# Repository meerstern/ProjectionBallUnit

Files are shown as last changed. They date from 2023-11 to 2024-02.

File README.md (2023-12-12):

# 簡易レーザープロジェクタ ProjectionBall Unit

## 概要 
  * ロボット制御技術を応用したガルバノスキャナ方式の簡易レーザープロジェクタです  
  * 文字や時刻、日時、内蔵図形を描画することが可能です  
  * 本体ボタン、PCのCOMポートやUARTを介して設定を変更することが可能です  
  * 任意の文字列は英数字を最大5文字同時表示、それ以上は32文字までスクロール表示可能です  
  * 投影距離は明るい場所で数m以下、暗い場所で10m以下が目安です  
  * Pico-SDKを使用したソースコードを公開しています  

## 仕様  
  * 電源スイッチ、モード切替、パターン切替、BOOTボタン、RESETボタンを搭載しています  
  * マイコンRP2040、RTC SD3077、モータFA-130、ドライバTB6612、エンコーダMA732Qを使用しています    
  * 赤色レーザーモジュール(出力1mW以下、ClassⅡ同等品)  
  * 5V/0.8AのUSB電源(micro USB)で動作  
  * 電源LED(青)、エラーLED(オレンジ)を搭載  
  * 時刻(RTC)/設定データ一時保存用電池 CR1220  
  * シリアルポートP1 ボーレート9600bps、データサイズ8bit、パリティ無、ストップ1bitが既定値
  * サイズ60mm x60mm x 43mm(突起部、USBコネクタ除く)、固定穴45mm x45mm M3x4

## アプリケーション例
  * 移動ロボットに組込して進路を表示  
  * イベント等での情報を表示  

## 注意点
  * この製品はclassⅡのレーザーを使用しています  
  * レーザーを使用しているため、光源を直視しないでください
  * 分解や改造をした状態で使用すると非常に危険ですので、お控えください  
  * この製品によって引き起こされることについては、当社は責任を持ちません  
  * 目にレーザー光が入る可能性があるため、人や動物に対して投影しないでください    
  * 汎用モータを使用しているため、描画のちらつきや崩れがあります    
  * ガルバノミラーはガラス製表面鏡のため、怪我をする恐れがあります 手を触れなでください  
  * 光軸がずれる可能性があるため、落下や衝撃を与えないでください  
  * 本製品は研究、開発目的の用途を想定しています  
  * 起動後にエラーLEDが点灯する場合はミラー部分が回転できるか、引っかかりがないか確認し、電源を入れ直してください    
  * 告知なしに部品や仕様を変更する場合があります  

## 使い方
### a.単体で使用する場合  
　microUSBをUSB電源等に接続し、電源スイッチ、モード切替、パターン切替スイッチで操作することが可能です    

### b.他の機器と連携する場合  
　microUSBをUSB電源等に接続し、P1端子を介してUART通信(ボーレート9600bps, 3.3V)可能です  
  マイコン等からコマンドを送信して制御することが可能です  

### c.設定を行う場合
　PC等にmicroUSBを接続し、Teraterm等からシリアルポートを介してコマンドで設定を行うことが可能です  

### d.ファームウェアの書換を行う場合
　PC等にmicroUSBを接続し、BOOTボタンを押した状態でRSTボタンを押すとUSBドライブとして認識されます  
  ファームウェアファイル(*.uf2)を認識されたUSBドライブに書き込むことでファームの書換が可能です  

## 描画モード

  * パターン0: 星
  * パターン1: 矢印
  * パターン2: メール
  * パターン3: スマイル
  * パターン4: 太陽
  * パターン5: 雲
  * パターン6: 傘
  * パターン7: 雪だるま
  * パターン8: 雲と雷
  * パターン9: ハート  

## 描画パターン   
  * モード0: 通常描画
  * モード1: 一筆書き描画
  * モード2: 回転描画
  * モード3: デジタル時計
  * モード4: デジタル日付
  * モード5: 任意メッセージ  
※メッセージは英数字、最大5文字、それ以上はスクロール表示です  

## 描画例
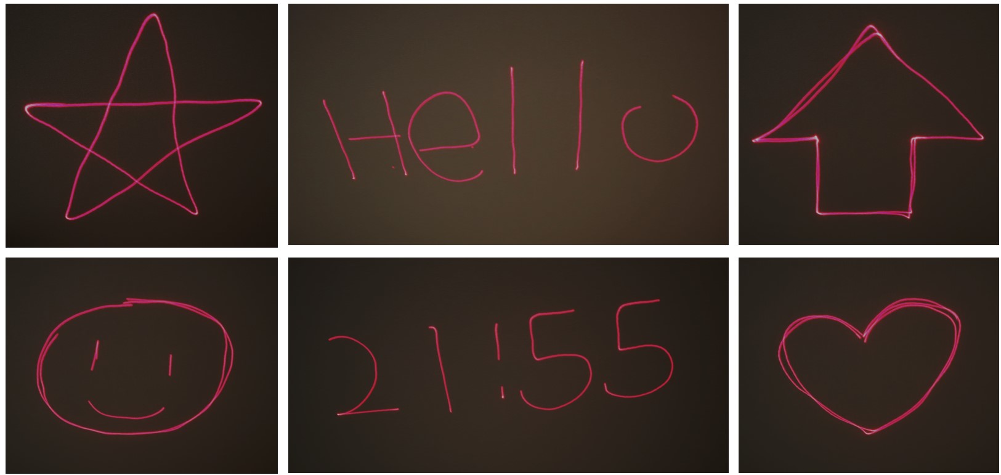
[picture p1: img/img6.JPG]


## 各部機能
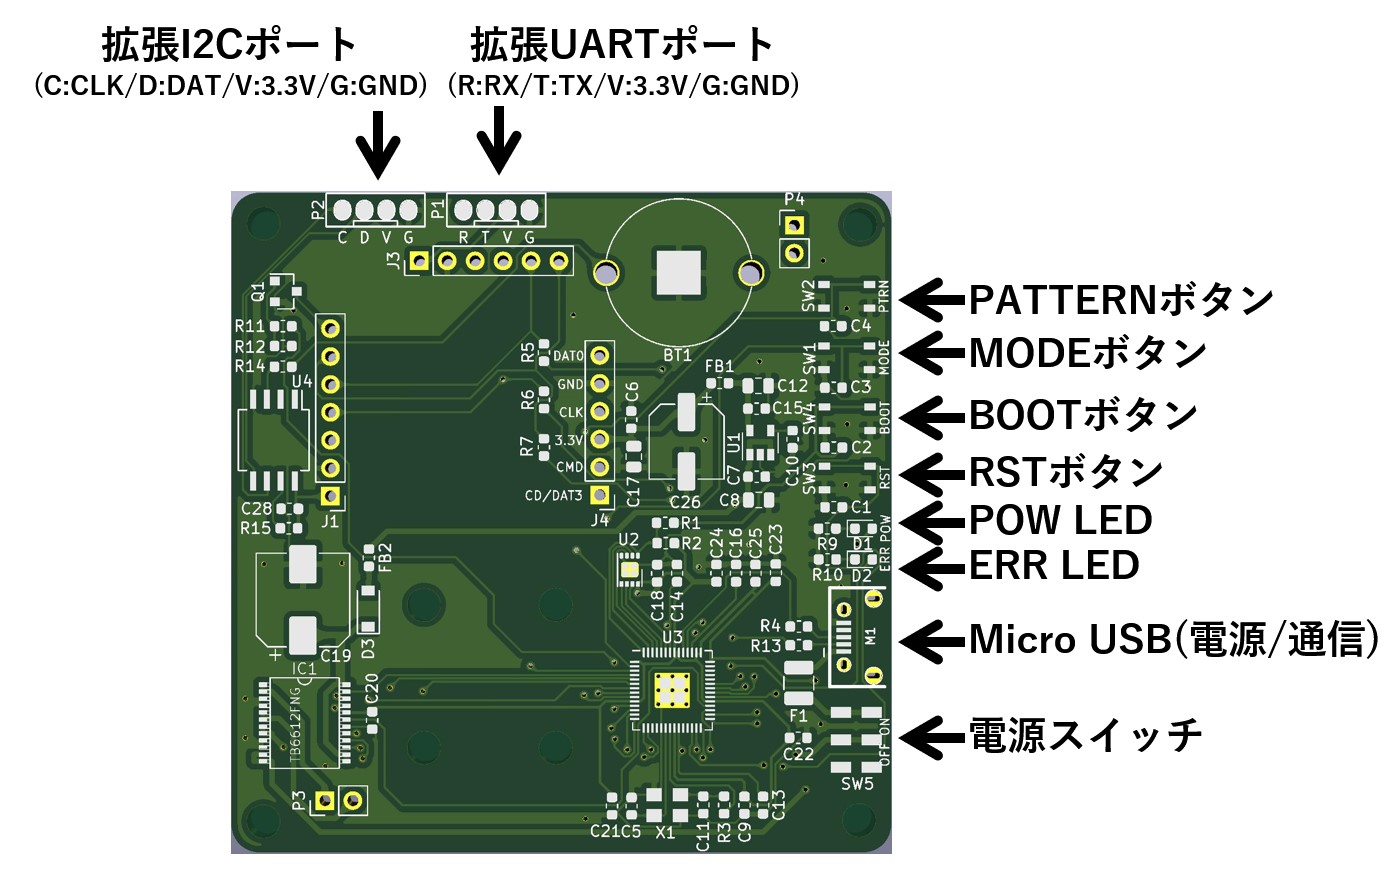
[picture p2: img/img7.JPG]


## コマンド
  * コマンド文字列を送信することで描画モードやパターン等の設定が可能です  
  * 改行コードは"\r\n"がデフォルトです  

### 日時設定コマンド  
| コマンド名 | コマンド | 引数 | 例 | 
|:---|:---|:---|:---|
| 時刻設定 | tim= | hhmmss | tim=220212(Enterキー) |
| 時刻確認 | tim? | なし | tim?(Enterキー) |
| 日時設定 |	day= | YYMMDD | day=220305(Enterキー) | 
| 日時確認 |	day? | なし | day?(Enterキー) | 	

※日付時刻は必ずそれぞれ2桁で入力してください  
　例　2時8分01秒→tim=020801 

### 制御コマンド  
| コマンド名 | コマンド | 引数 | 例 | 
|:---|:---|:---|:---|
| モード確認 |	mod? | なし | mod?(Enterキー) | 
| モード設定 |	mod= | モード | mod=1(Enterキー) | 
| パターン確認 |	ptn? | なし | ptn?(Enterキー) | 
| パターン設定 |	ptn= | パターン| ptn=2(Enterキー) | 
| ソフトリセット | rst! | なし | rst!(Enterキー) |  
| 描画一時停止 | pus! | なし | pus!(Enterキー) |
| 描画再開 |	rsm! | なし | rsm!(Enterキー) | 
| 描画角設定 |	deg= | 角度 | deg=90(Enterキー) | 	
| 描画角確認 |	deg? | なし | deg?(Enterキー) | 	

※描画角は描画の上下左右等の角度を変更する場合に使用します  
※描画角のデフォルトは0度(deg=0)です  

### ユーザ設定コマンド  
| コマンド名 | コマンド | 引数 | 例 | 
|:---|:---|:---|:---|
| 描画文字列確認 |	str? | なし | str?(Enterキー) | 
| 描画文字列設定(MEM) |	str= | 英数字 | str=Hello(Enterキー) | 
| 描画文字列設定(RAM) |	stg= | 英数字 | stg=Hello(Enterキー) |  

※MEMの場合、文字列はメモリに保存され、自動的に再起動します  
※RAMの場合、文字列は即時反映されますが、電源再投入等でメモリに保存された文字列に戻ります  

### タイマ設定コマンド  
| コマンド名 | コマンド | 引数 | 例 | 
|:---|:---|:---|:---|
| タイマ確認 |	tst? | なし | tst?(Enterキー) | 
| タイマ有効化 | ten! | なし | ten!(Enterキー) |  
| タイマ無効化 | tds! | なし | tds!(Enterキー) |
| 停止時刻確認 |	pus? | なし | pus?(Enterキー) | 
| 停止時刻設定 |	pus= | hhmm | pus=1230(Enterキー) | 
| 再開時刻確認 |	rsm? | なし | pus?(Enterキー) | 
| 再開時刻設定 |	rsm= | hhmm | pus=1530(Enterキー) | 

※タイマ確認は0で無効状態、1で有効状態を示しています  

### キャリブレーションコマンド  
| コマンド名 | コマンド | 引数 | 例 | 
|:---|:---|:---|:---|
| 描画中心確認 |	cen? | なし | cen?(Enterキー) | 
| 描画中心設定 |	cen= | X,Y | cen=100,-200(Enterキー) | 

※レーザーが基板や筐体に当たって描画が隠れてしまう場合にのみ、描画中心を調整します  
※描画中心のキャリブレーション値は出荷時に調整しています    
※キャリブレーション値は初期値に対してX軸(縦方向)、Y軸(横方向)のオフセット値を設定します  

### エラーLED点灯時の確認
  * 起動後にエラーLEDが点灯する場合はミラー部分が回転できるか、引っかかりがないか確認し、電源を入れ直してください
  * ミラーが回転して描画を開始しない場合は下記の図のようにミラーの角度を調整して電源を入れ直してください
  * 手前から見てレーザーモジュールからの光がX軸ミラー、Y軸ミラーの2つのミラーに反射する角度に調整します  
  * ミラーはガラス製のため、怪我の恐れがあります  手を触れないように注意してください   
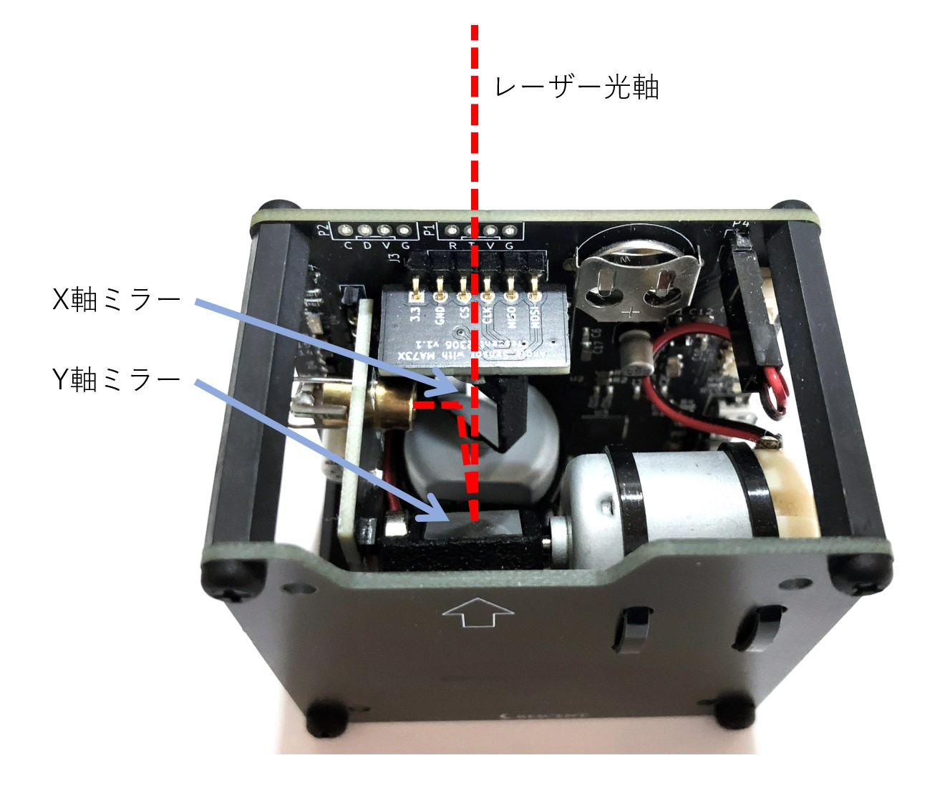
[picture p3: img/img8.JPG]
  

### 電池交換時の確認
  * RTC電池は電源供給なしで3年以上、日時、時刻及び設定情報を保持することが可能です
  * 万一、保持できなくなった場合はCR1220の電池交換を行ってください
  * 設定情報はモード、パターン、タイマ状態、描画角を保持しています
  * 電池交換後は日時、時刻及び設定情報が不定値となるため、必ず時刻、日付、モード、パターン、タイマ状態、描画角を再設定してください  
  * 特に描画角が不定値になると正しく描画されません deg=0(Enterキー)とコマンドを入力して設定してください

## 外観
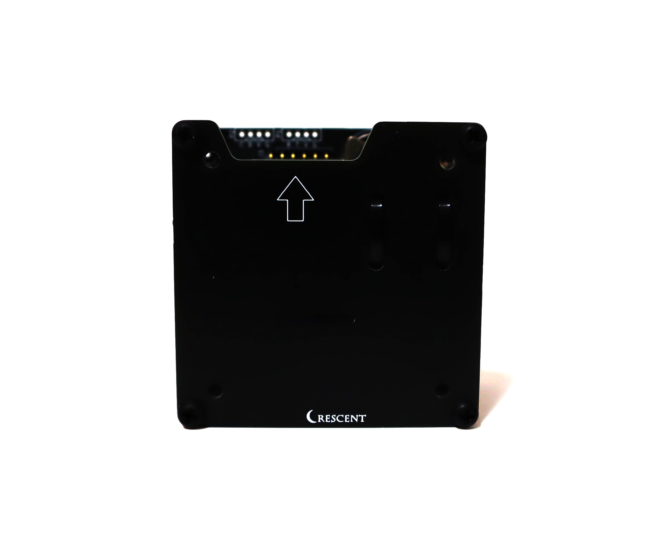
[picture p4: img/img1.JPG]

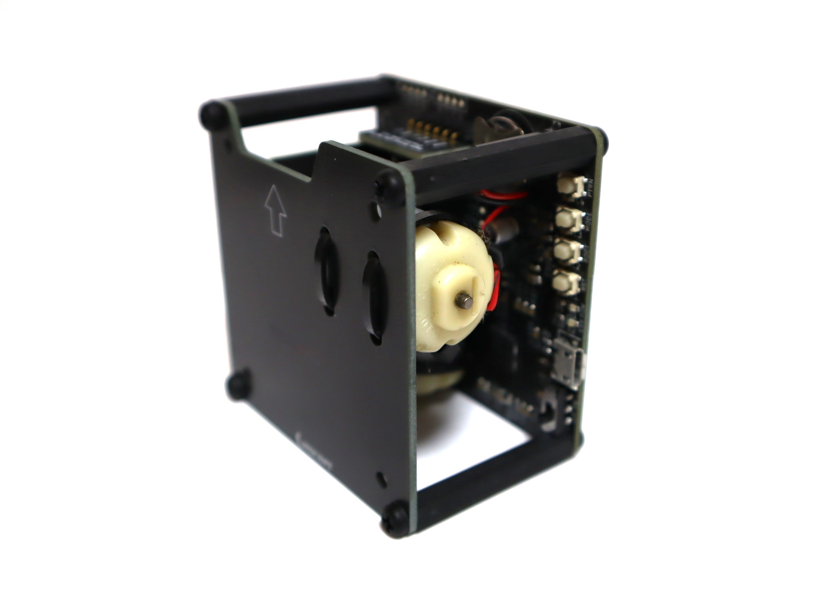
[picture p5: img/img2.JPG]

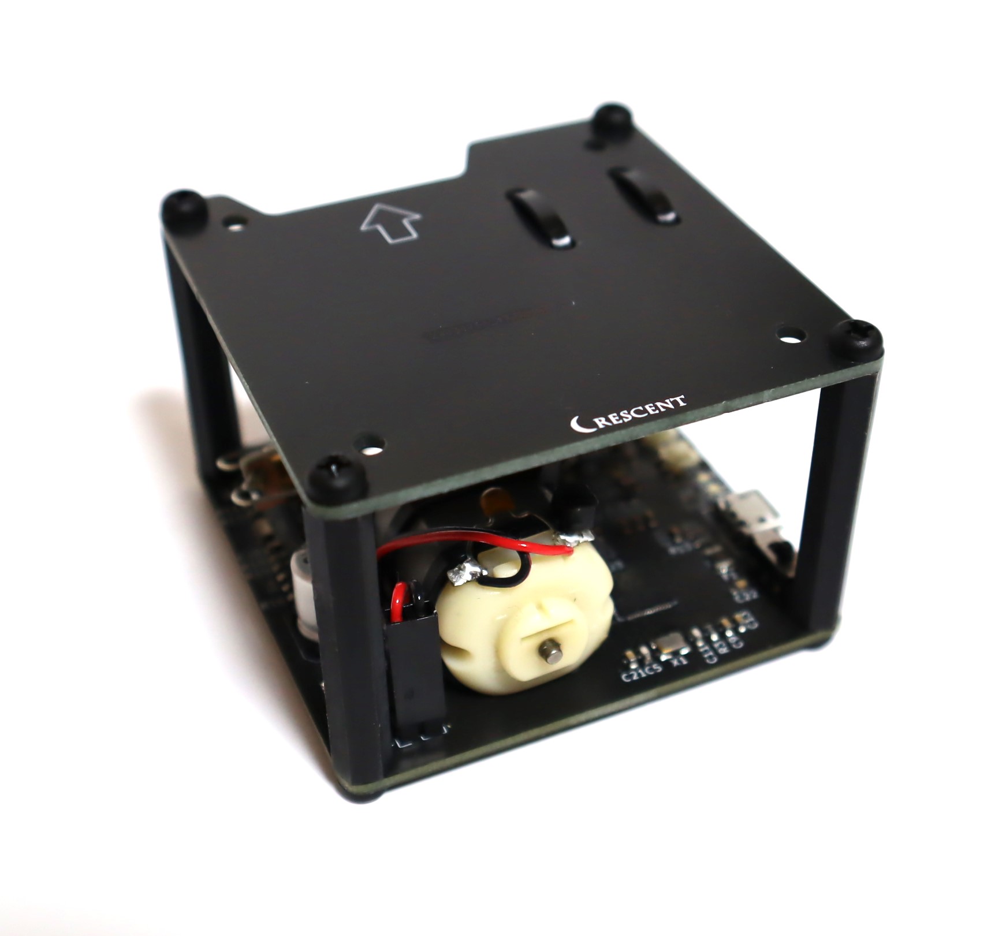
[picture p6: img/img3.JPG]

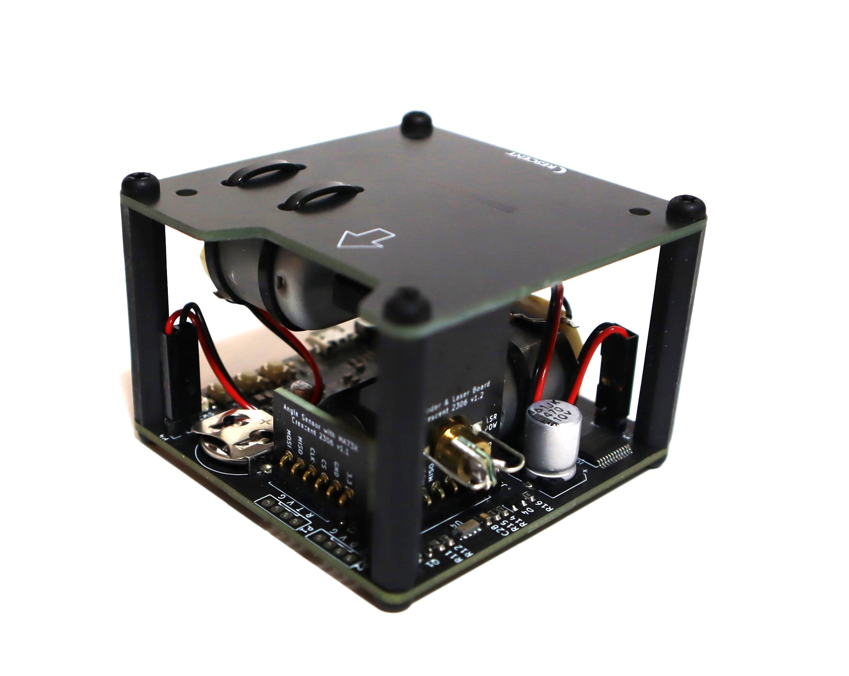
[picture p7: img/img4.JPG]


License - MIT

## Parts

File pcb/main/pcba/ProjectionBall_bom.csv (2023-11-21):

Comment | Designator | Footprint | LCSC part number | Stock
SW_DPDT_x2 | SW5 | DPDT_SMD_Large | C115375
SD3077 | U4 | SO-8_5.3x6.2mm_P1.27mm | C4748679
27 | R7,R6,R5,R13,R4 | R_0603_1608Metric | C227752
100u | C26 | CP_Elec_6.3x3.9 | C2963046
Q_NMOS_GSD | Q1 | SOT-23 | C2991132
Ferrite_Bead_Small | FB2,FB1 | L_0603_1608Metric | C80165
10u | C17,C12,C8 | C_0805_2012Metric | C380332
0.1u | C14,C28,C25,C24,C23,C22,C21,C18,C13,C9,C2,C1,C3,C4,C6,C7,C15,C20 | C_0603_1608Metric | C56476
W25Q16JVUX | U2 | SON-8-1EP_3x2mm_P0.5mm_EP1.4x1.6mm | C2843335
RP2040 | U3 | RP2040-QFN-56 | C2040
12MHz | X1 | FA238V | C2901650
SW_Push | SW4,SW3,SW1,SW2 | SKRPACE010 | C115360
10k | R15,R2,R12 | R_0603_1608Metric | C209220
330 | R14 | R_0603_1608Metric | C103548
1k | R3,R1,R9,R10,R11 | R_0603_1608Metric | C73797
2.2u | C16 | C_0603_1608Metric | C2691406
10p | C11,C5 | C_0603_1608Metric | C388068
0.01u | C10 | C_0603_1608Metric | C307346
470u | C19 | CP_Elec_8x10 | C2827943
POW_LED | D1 | LED_0603_1608Metric | C89814
ERR_LED | D2 | LED_0603_1608Metric | C90692
Fuse | F1 | R_1210_3225Metric | C20805
TB6612FNG | IC1 | tb6612-SSOP24 | C141517
MICRO-USB-SHIELD-ZX62R-B-5P | M1 | CONN-10118194-0001LF-FCI | C132563
LD3985M33R | U1 | SOT-23-5 | C46243
D | D3 | D_SOD-123 | C129191

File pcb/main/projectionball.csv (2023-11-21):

ID | 参照記号 | パッケージ | 数 | 名称 | Supplier and ref
1 | SW5 | DPDT_SMD_Large | 1 | SW_DPDT_x2
2 | U4 | SO-8_5.3x6.2mm_P1.27mm | 1 | SD3077
3 | R7,R6,R5,R13,R4 | R_0603_1608Metric | 5 | 27
4 | C26 | CP_Elec_6.3x3.9 | 1 | 100u
5 | Q1 | SOT-23 | 1 | Q_NMOS_GSD
6 | J4 | PinHeader_1x06_P2.54mm_Vertical | 1 | microTF
7 | FB2,FB1 | L_0603_1608Metric | 2 | Ferrite_Bead_Small
8 | P2 | GROVE | 1 | GROVE_I2C
9 | P1 | GROVE | 1 | GROVE_UART
10 | P4 | PinHeader_1x02_P2.54mm_Vertical | 1 | MOTOR2
11 | J1 | PinHeader_1x07_P2.54mm_Vertical | 1 | Conn_01x07
12 | C17,C12,C8 | C_0805_2012Metric | 3 | 10u
13 | C14,C28,C25,C24,C23,C22,C21,C18,C13,C9,C2,C1,C3,C4,C6,C7,C15,C20 | C_0603_1608Metric | 18 | 0.1u
14 | U2 | SON-8-1EP_3x2mm_P0.5mm_EP1.4x1.6mm | 1 | W25Q16JVUX
15 | U3 | RP2040-QFN-56 | 1 | RP2040
16 | X1 | FA238V | 1 | 12MHz
17 | SW4,SW3,SW1,SW2 | SKRPACE010 | 4 | SW_Push
18 | R15,R2 | R_0603_1608Metric | 2 | 10k
19 | R14 | R_0603_1608Metric | 1 | 330
20 | R3,R1,R9,R10,R11 | R_0603_1608Metric | 5 | 1k
21 | C16 | C_0603_1608Metric | 1 | 2.2u
22 | C11,C5 | C_0603_1608Metric | 2 | 10p
23 | BT1 | 2895 | 1 | CR1220
24 | REF3,REF4,REF2,REF1,REF12,REF11,REF10,REF9 | MountingHole_3mm | 8 | MountingHole_3mm
25 | C10 | C_0603_1608Metric | 1 | 0.01u
26 | C19 | CP_Elec_8x10 | 1 | 470u
27 | D1 | LED_0603_1608Metric | 1 | POW_LED
28 | D2 | LED_0603_1608Metric | 1 | ERR_LED
29 | F1 | R_1210_3225Metric | 1 | Fuse
30 | IC1 | tb6612-SSOP24 | 1 | TB6612FNG
31 | J3 | PinHeader_1x06_P2.54mm_Vertical | 1 | ENC1
32 | M1 | CONN-10118194-0001LF-FCI | 1 | MICRO-USB-SHIELD-ZX62R-B-5P
33 | P3 | PinHeader_1x02_P2.54mm_Vertical | 1 | MOTOR1
34 | R12 | R_0603_1608Metric | 1 | 20k
35 | U1 | SOT-23-5 | 1 | LD3985M33R
36 | D3 | D_SOD-123 | 1 | D

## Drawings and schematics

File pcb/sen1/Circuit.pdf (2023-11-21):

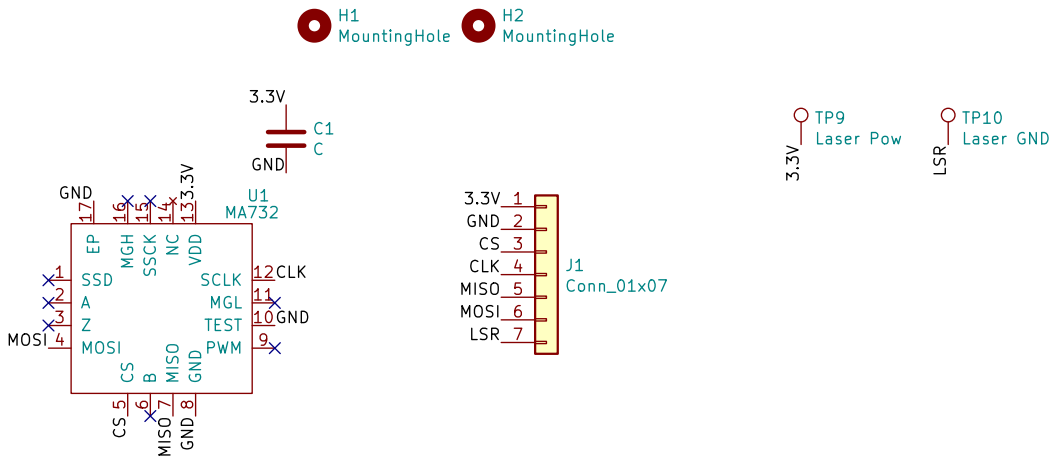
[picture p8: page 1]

CS CLK MISO MOSI C1 C GND

File: ma73x.sch Sheet: / Crescent

Id: 1/1 Title: ProjectionBall Encoder & Laser Board

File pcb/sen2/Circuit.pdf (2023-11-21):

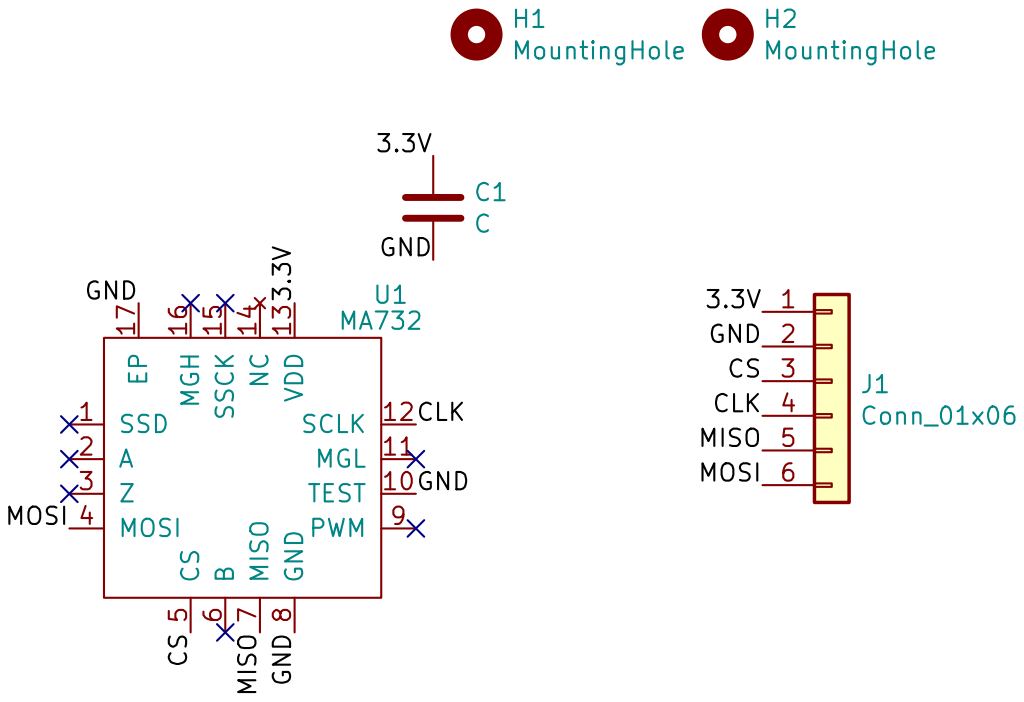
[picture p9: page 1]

CS CLK MISO MOSI C1 C GND

File: ma73x.sch Sheet: / Crescent

Id: 1/1 Title: Angle Sensor Board with MA732

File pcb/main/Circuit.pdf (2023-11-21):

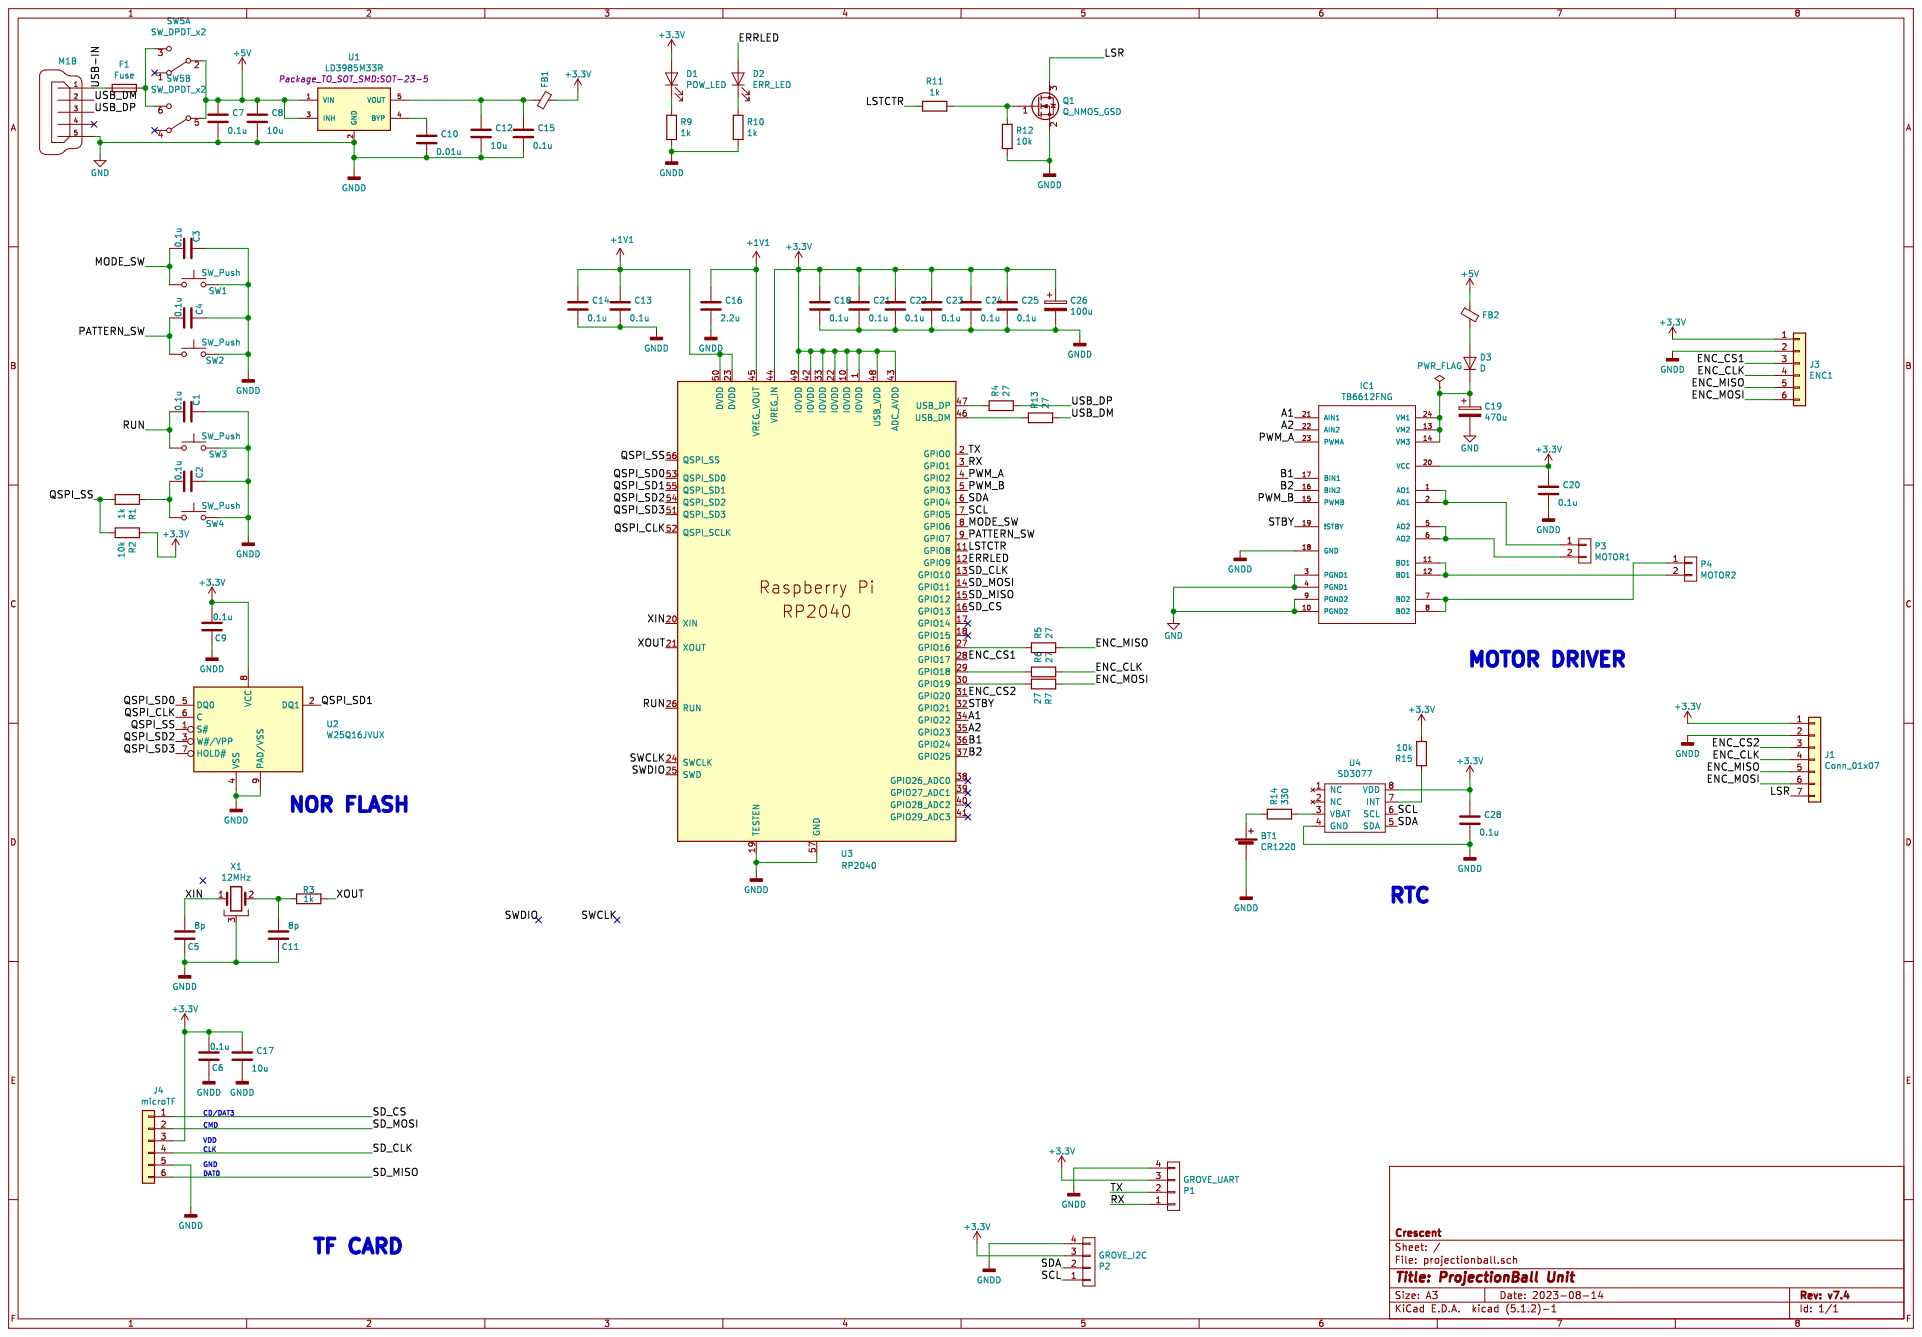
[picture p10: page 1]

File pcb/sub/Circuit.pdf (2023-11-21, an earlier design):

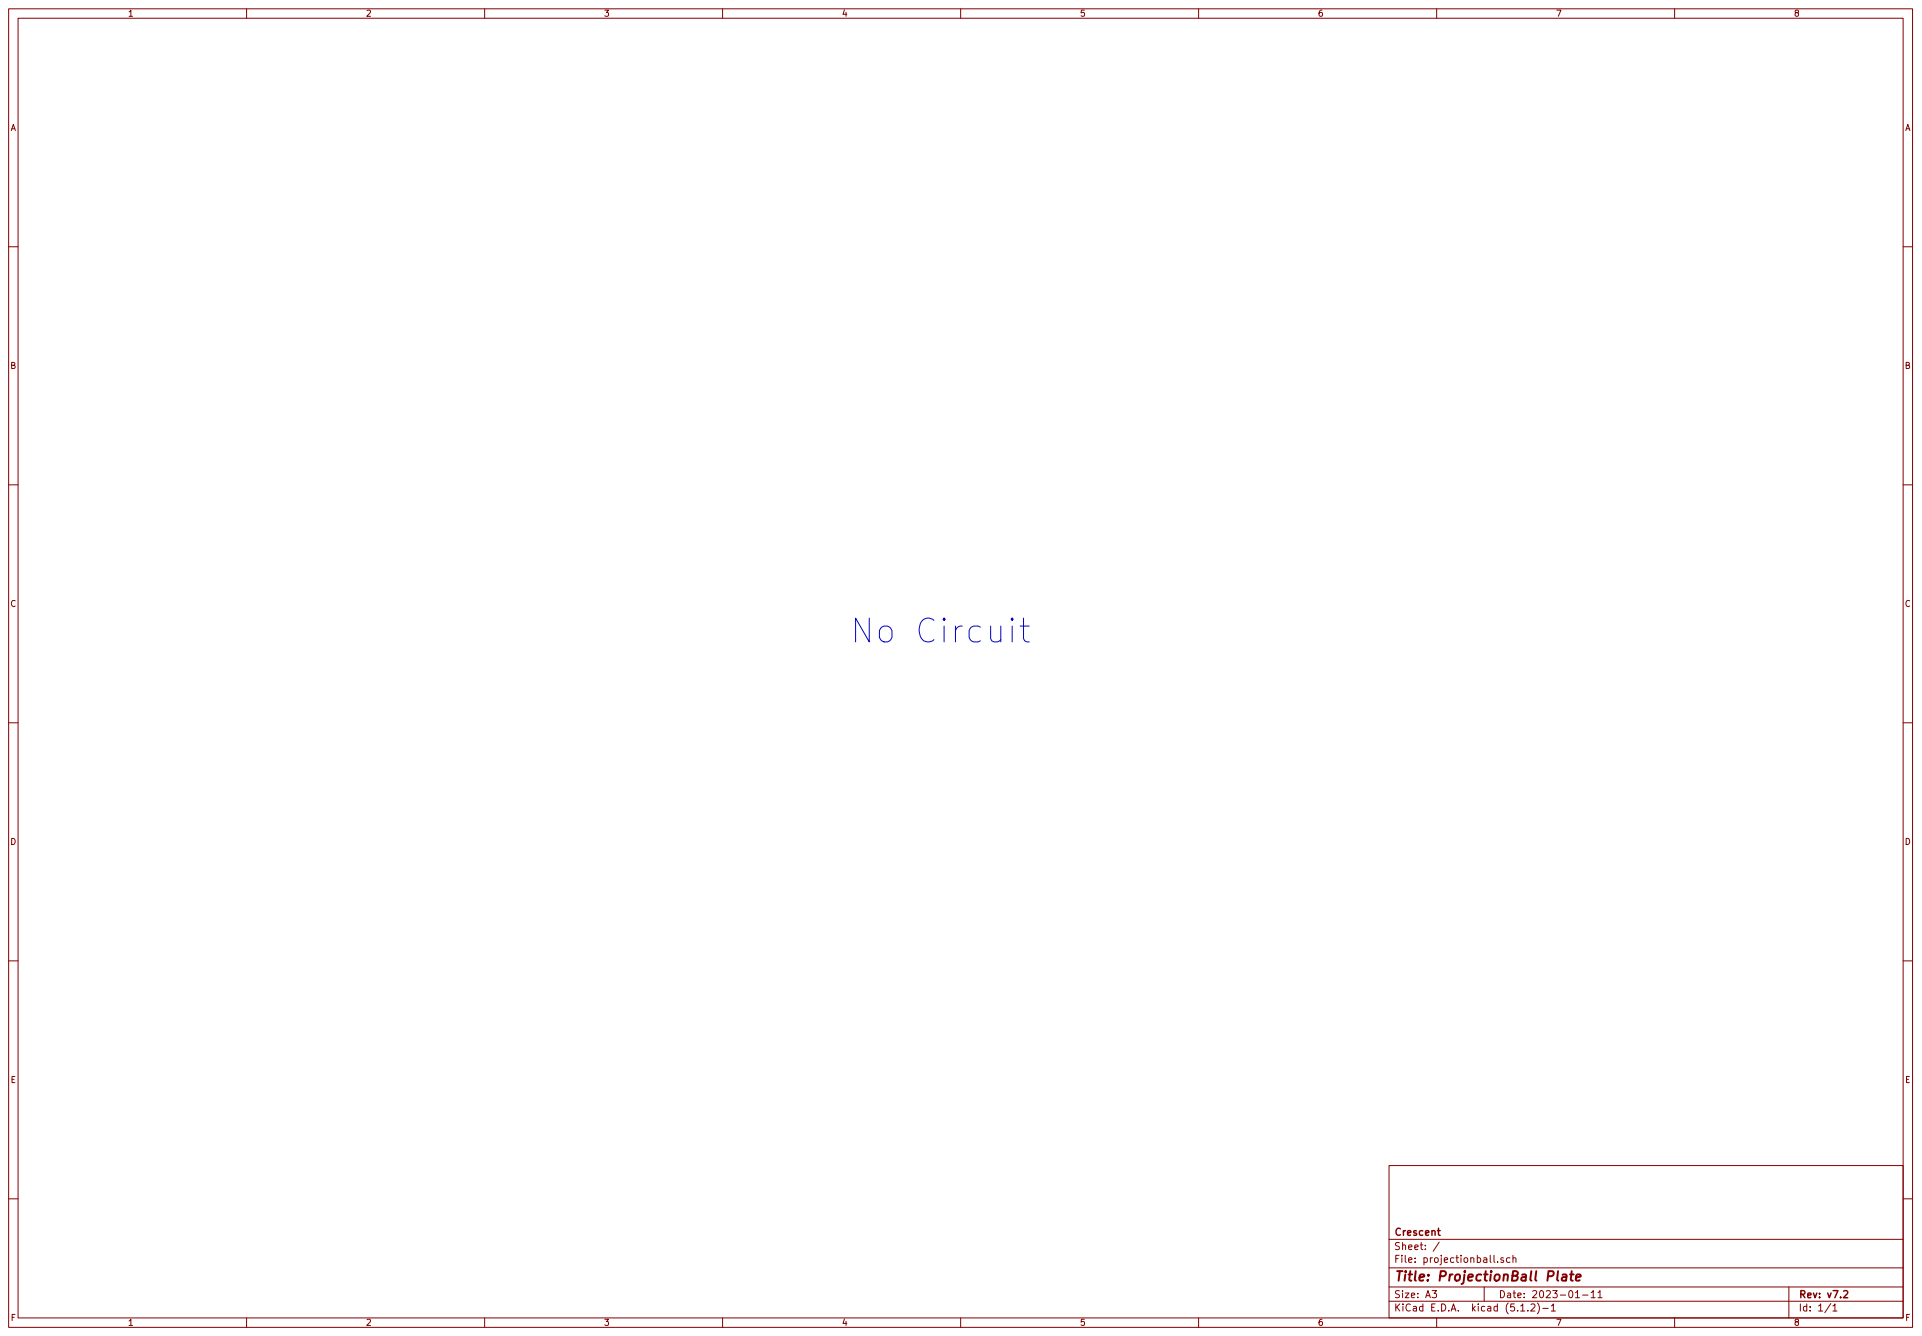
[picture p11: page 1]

File: projectionball.sch Sheet: / Crescent No Circuit

Id: 1/1 Title: ProjectionBall Plate

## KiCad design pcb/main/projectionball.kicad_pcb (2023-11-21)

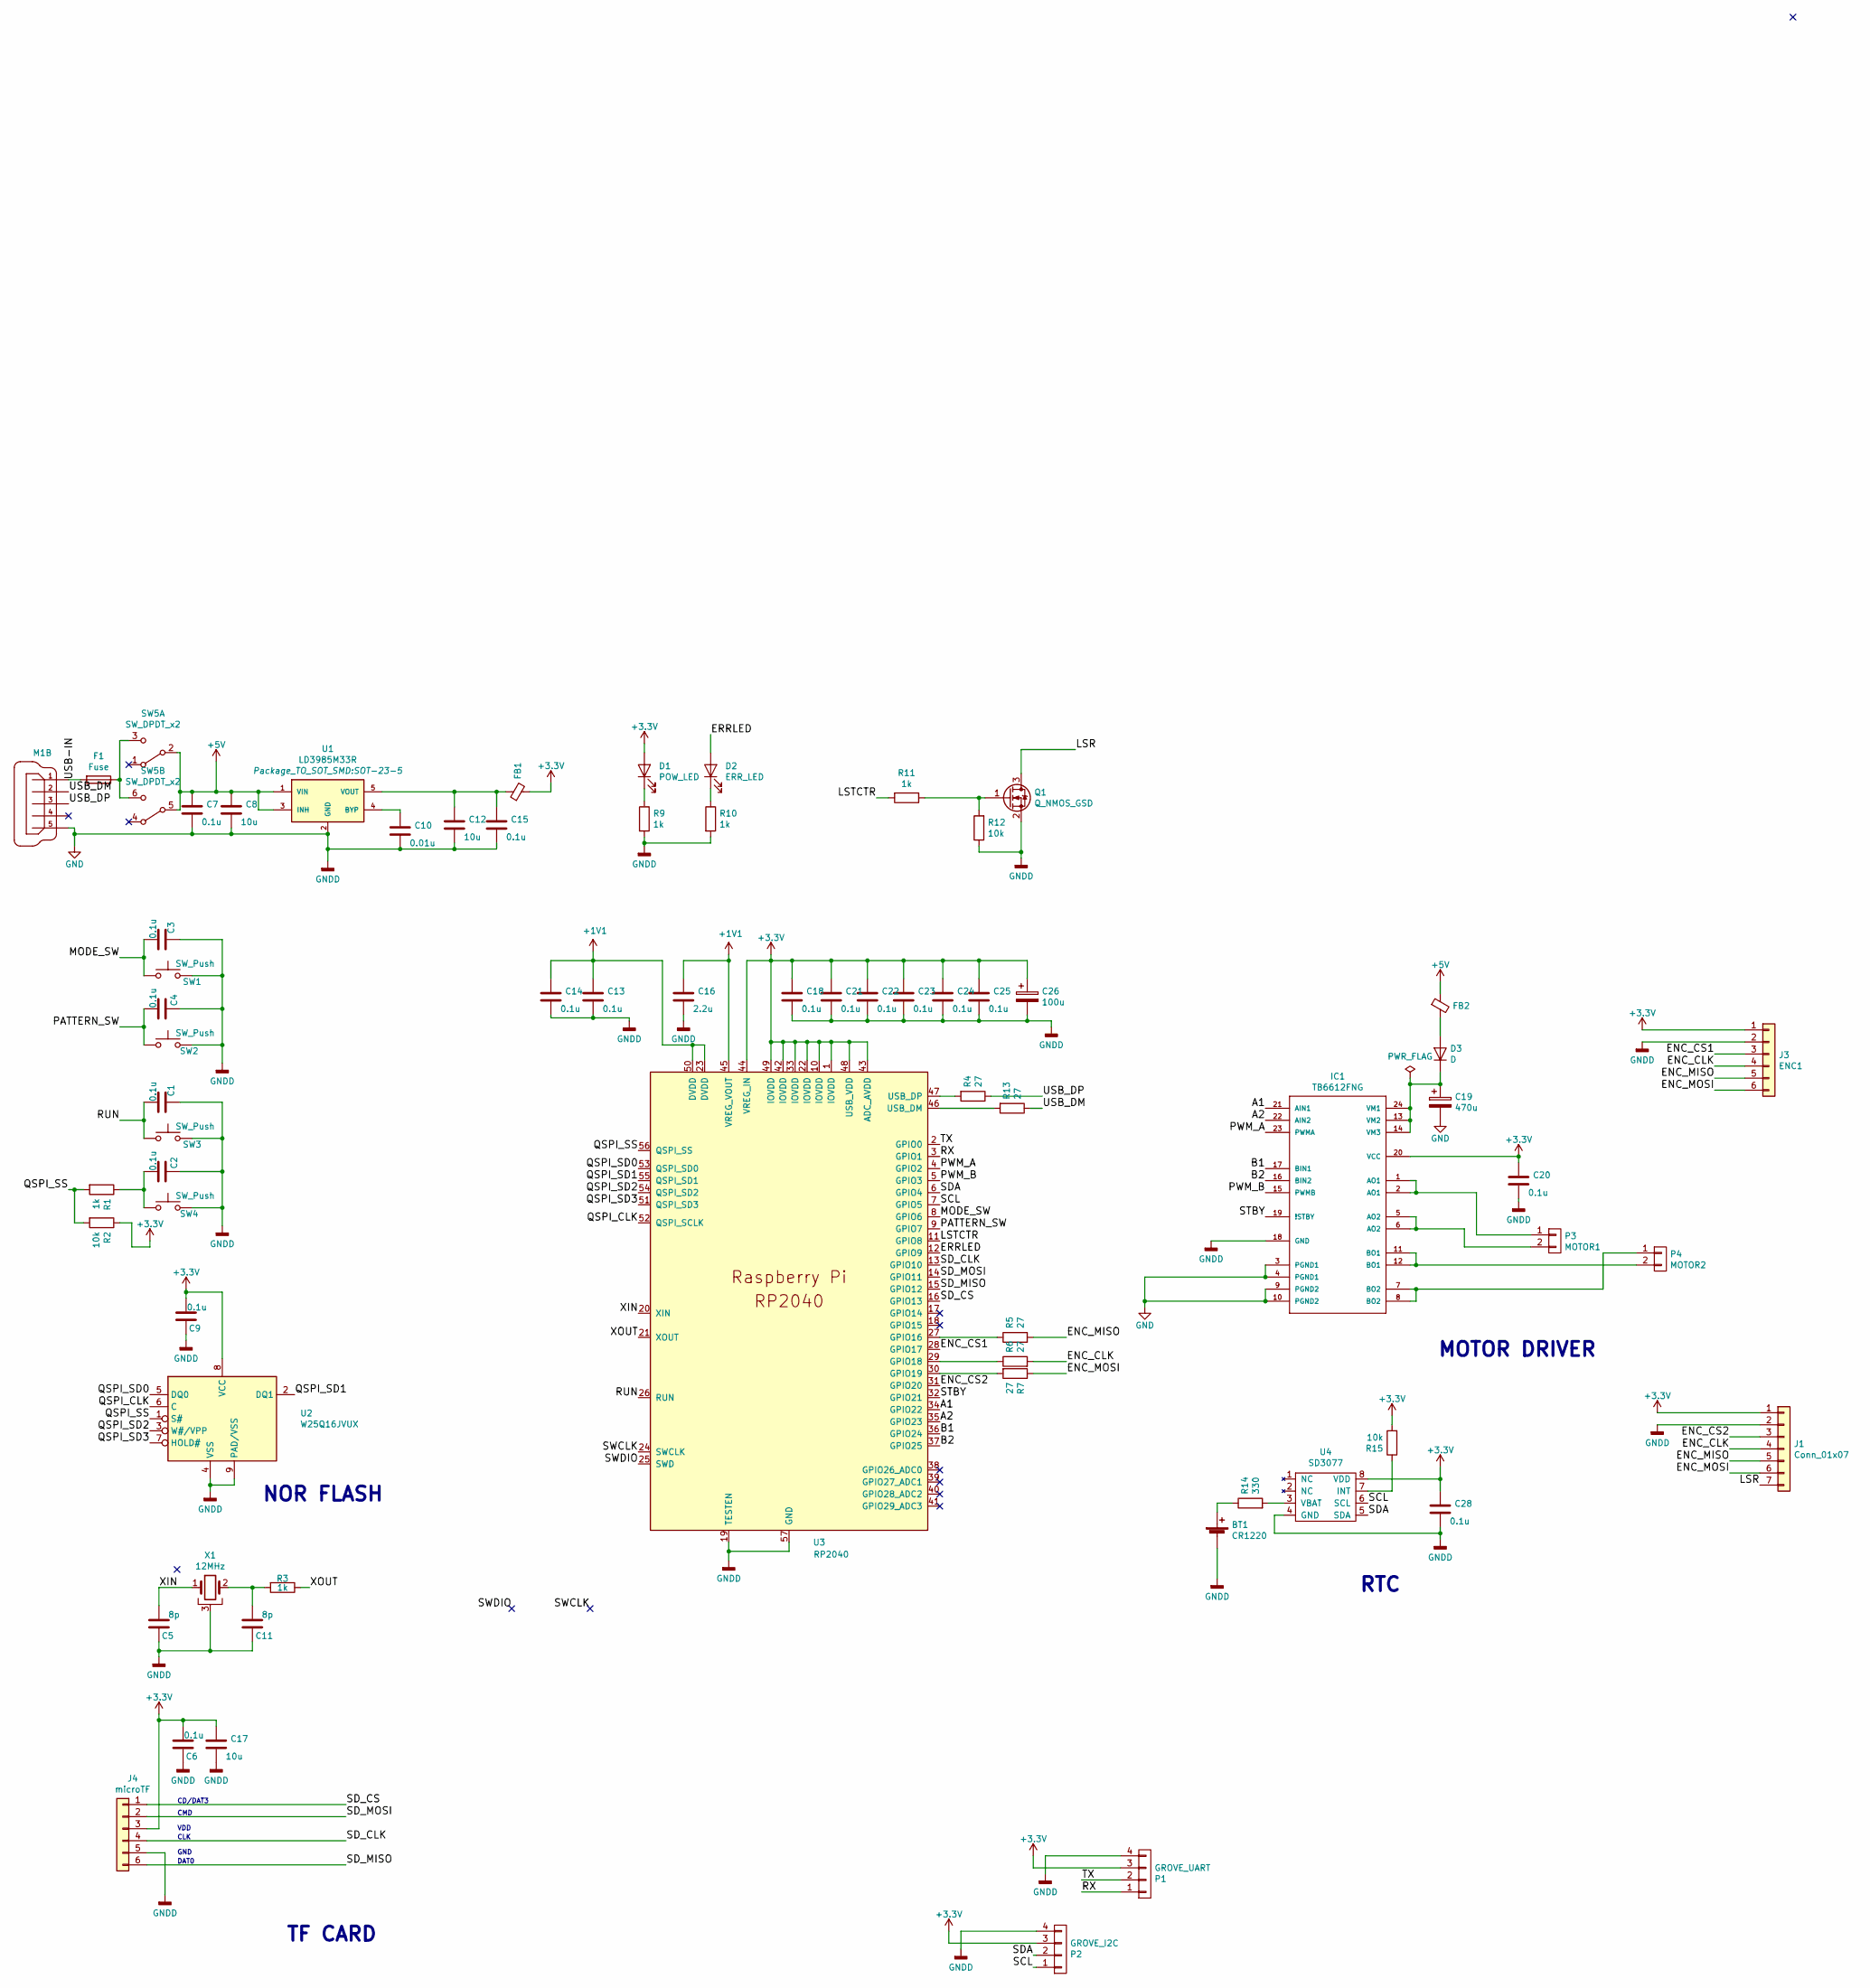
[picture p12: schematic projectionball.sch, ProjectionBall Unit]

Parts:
BT1: CR1220; 2895
C1, C2, C3, C4, C6, C7, C9, C13, C14, C15, C18, C20, C21, C22, C23, C24, C25, C28: 0.1u; C_0603_1608Metric
C5, C11: 8p; C_0603_1608Metric
C8, C12, C17: 10u; C_0805_2012Metric
C10: 0.01u; C_0603_1608Metric
C16: 2.2u; C_0603_1608Metric
C19: 470u; CP_Elec_8x10
C26: 100u; CP_Elec_6.3x3.9
D1: POW_LED; LED_0603_1608Metric
D2: ERR_LED; LED_0603_1608Metric
D3: D; D_SOD-123
F1: Fuse; R_1210_3225Metric
FB1, FB2: Ferrite_Bead_Small; L_0603_1608Metric
IC1: TB6612FNG; tb6612-SSOP24
J1: Conn_01x07; PinHeader_1x07_P2.54mm_Vertical
J3: ENC1; PinHeader_1x06_P2.54mm_Vertical
J4: microTF; PinHeader_1x06_P2.54mm_Vertical
M1: MICRO-USB-SHIELD-ZX62R-B-5P; CONN-10118194-0001LF-FCI
P1: GROVE_UART; GROVE
P2: GROVE_I2C; GROVE
P3: MOTOR1; PinHeader_1x02_P2.54mm_Vertical
P4: MOTOR2; PinHeader_1x02_P2.54mm_Vertical
Q1: Q_NMOS_GSD; SOT-23
R1, R3, R9, R10, R11: 1k; R_0603_1608Metric
R2, R12, R15: 10k; R_0603_1608Metric
R4, R5, R6, R7, R13: 27; R_0603_1608Metric
R14: 330; R_0603_1608Metric
SW1, SW2, SW3, SW4: SW_Push; SKRPACE010
SW5: SW_DPDT_x2; DPDT_SMD_Large
U1: LD3985M33R; SOT-23-5
U2: W25Q16JVUX; SON-8-1EP_3x2mm_P0.5mm_EP1.4x1.6mm
U3: RP2040; RP2040-QFN-56
U4: SD3077; SO-8_5.3x6.2mm_P1.27mm
X1: 12MHz; FA238V

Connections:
+1V1: C13.1, C14.1, C16.1, U3.23 (DVDD), U3.45 (VREG_VOUT), U3.50 (DVDD)
+3V3: C6.2, C9.2, C17.1, C18.1, C20.1, C21.1, C22.1, C23.1, C24.1, C25.1, C26.1, C28.1, D1.2 (A), FB1.2, IC1.20 (VCC), J1.1, J3.1, J4.3, P1.3, P2.3, R2.1, R15.2, U2.8 (VCC), U3.1 (IOVDD), U3.10 (IOVDD), U3.22 (IOVDD), U3.33 (IOVDD), U3.42 (IOVDD), U3.43 (ADC_AVDD), U3.44 (VREG_IN), U3.48 (USB_VDD), U3.49 (IOVDD), U4.8 (VDD)
+5V: C7.1, C8.1, FB2.1, SW5.2 (B), SW5.5 (B), U1.1 (VIN), U1.3 (INH)
/A1: IC1.21 (AIN1), U3.34 (GPIO22)
/A2: IC1.22 (AIN2), U3.35 (GPIO23)
/B1: IC1.17 (BIN1), U3.36 (GPIO24)
/B2: IC1.16 (BIN2), U3.37 (GPIO25)
/ENC_CLK: J1.4, J3.4, R6.2
/ENC_CS1: J3.3, U3.28 (GPIO17)
/ENC_CS2: J1.3, U3.31 (GPIO20)
/ENC_MISO: J1.5, J3.5, R5.2
/ENC_MOSI: J1.6, J3.6, R7.1
/ERRLED: D2.2 (A), U3.12 (GPIO9)
/LSR: J1.7, Q1.3 (D)
/LSTCTR: R11.2, U3.11 (GPIO8)
/MODE_SW: C3.2, SW1.1, U3.8 (GPIO6)
/PATTERN_SW: C4.2, SW2.1, U3.9 (GPIO7)
/PWM_A: IC1.23 (PWMA), U3.4 (GPIO2)
/PWM_B: IC1.15 (PWMB), U3.5 (GPIO3)
/QSPI_CLK: U2.6 (C), U3.52 (QSPI_SCLK)
/QSPI_SD0: U2.5 (DQ0), U3.53 (QSPI_SD0)
/QSPI_SD1: U2.2 (DQ1), U3.55 (QSPI_SD1)
/QSPI_SD2: U2.3 (W#/VPP), U3.54 (QSPI_SD2)
/QSPI_SD3: U2.7 (HOLD#), U3.51 (QSPI_SD3)
/QSPI_SS: R1.2, R2.2, U2.1 (S#), U3.56 (QSPI_SS)
/RUN: C1.2, SW3.1, U3.26 (RUN)
/RX: P1.1, U3.3 (GPIO1)
/SCL: P2.1, U3.7 (GPIO5), U4.6 (SCL)
/SDA: P2.2, U3.6 (GPIO4), U4.5 (SDA)
/SD_CLK: J4.4, U3.13 (GPIO10)
/SD_CS: J4.1, U3.16 (GPIO13)
/SD_MISO: J4.6, U3.15 (GPIO12)
/SD_MOSI: J4.2, U3.14 (GPIO11)
/STBY: IC1.19 (!STBY), U3.32 (GPIO21)
/TX: P1.2, U3.2 (GPIO0)
/USB-IN: F1.2, M1.1
/USB_DM: M1.2, R13.1
/USB_DP: M1.3, R4.1
/XIN: C5.2, U3.20 (XIN), X1.1
/XOUT: R3.1, U3.21 (XOUT)
GND: BT1.2 (-), C1.1, C2.1, C3.1, C4.1, C5.1, C6.1, C7.2, C8.2, C9.1, C10.2, C11.1, C12.2, C13.2, C14.2, C15.2, C16.2, C17.2, C18.2, C19.2, C20.2, C21.2, C22.2, C23.2, C24.2, C25.2, C26.2, C28.2, IC1.3 (PGND1), IC1.4 (PGND1), IC1.9 (PGND2), IC1.10 (PGND2), IC1.18 (GND), J1.2, J3.2, J4.5, M1.5, P1.4, P2.4, Q1.2 (S), R9.2, R10.2, R12.1, SW1.2, SW2.2, SW3.2, SW4.2, U1.2 (GND), U2.4 (VSS), U2.9 (PAD/VSS), U3.19 (TESTEN), U3.57 (GND), U4.4 (GND), X1.3
unnamed: BT1.1 (+), R14.1
unnamed: C2.2, R1.1, SW4.1
unnamed: C10.1, U1.4 (BYP)
unnamed: C11.2, R3.2, X1.2
unnamed: C12.1, C15.1, FB1.1, U1.5 (VOUT)
unnamed: C19.1, D3.1 (K), IC1.13 (VM2), IC1.14 (VM3), IC1.24 (VM1)
unnamed: D1.1 (K), R9.1
unnamed: D2.1 (K), R10.1
unnamed: D3.2 (A), FB2.2
unnamed: F1.1, SW5.3 (C), SW5.6 (C)
unnamed: IC1.1 (AO1), IC1.2 (AO1), P3.1
unnamed: IC1.5 (AO2), IC1.6 (AO2), P3.2
unnamed: IC1.7 (BO2), IC1.8 (BO2), P4.1
unnamed: IC1.11 (BO1), IC1.12 (BO1), P4.2
unnamed: Q1.1 (G), R11.1, R12.2
unnamed: R4.2, U3.47 (USB_DP)
unnamed: R5.1, U3.27 (GPIO16)
unnamed: R6.1, U3.29 (GPIO18)
unnamed: R7.2, U3.30 (GPIO19)
unnamed: R13.2, U3.46 (USB_DM)
unnamed: R14.2, U4.3 (VBAT)
unnamed: R15.1, U4.7 (INT)

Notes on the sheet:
RTC
MOTOR DRIVER
TF CARD
NOR FLASH
CD/DAT3
CMD
VDD
CLK
GND
DAT0

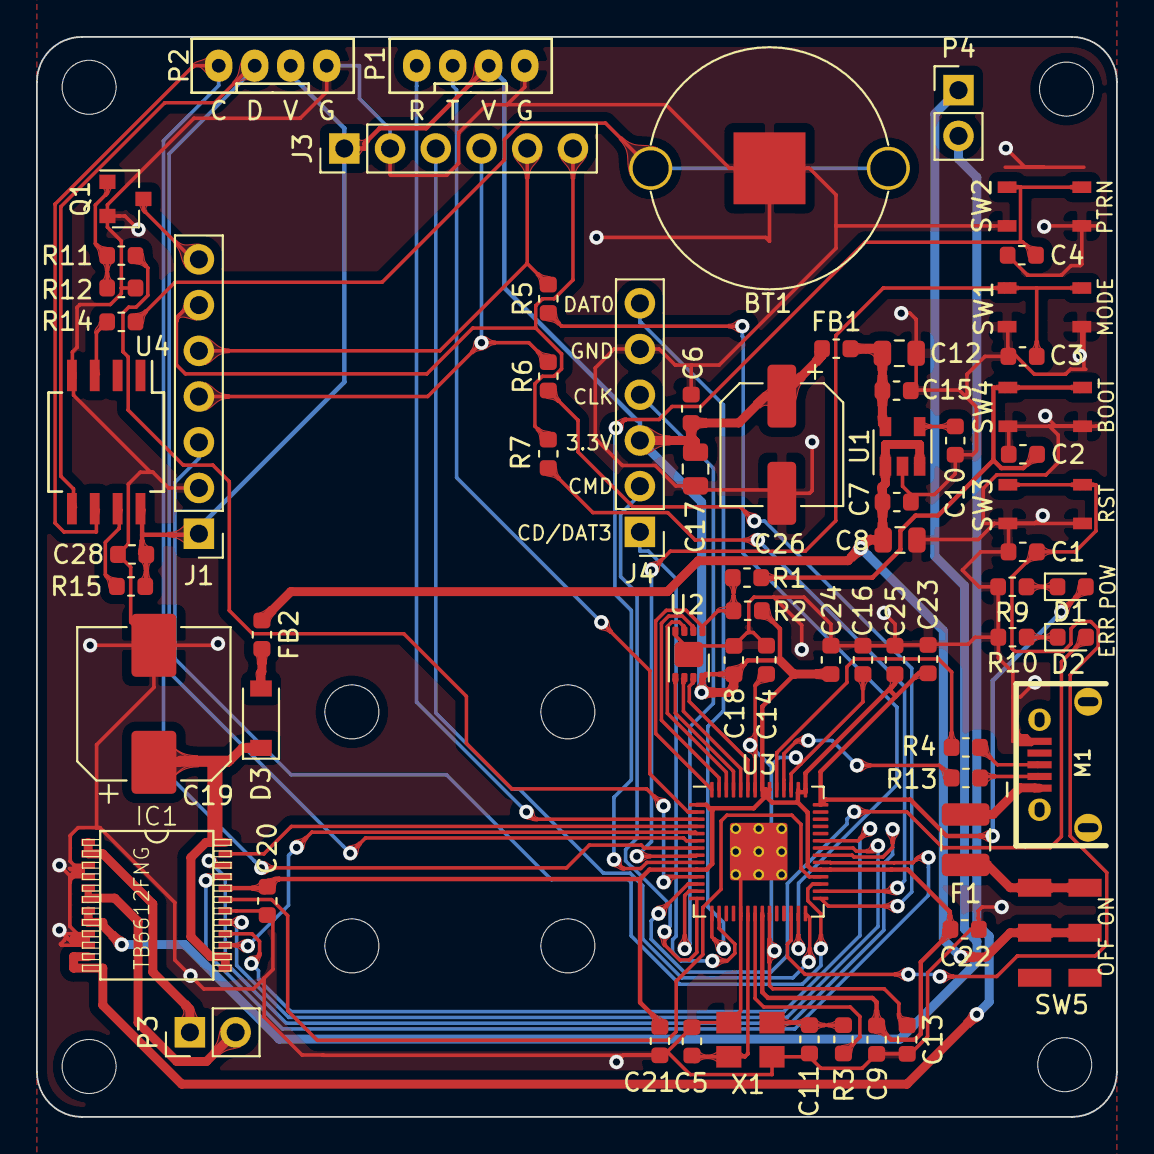
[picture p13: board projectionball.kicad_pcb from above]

Board: 2 copper layers, 60.0 x 60.0 mm, 76 parts (0 on the bottom side), 63 nets.

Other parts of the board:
REF1, REF2, REF3, REF4, REF9, REF10, REF11, REF12: MountingHole_3mm

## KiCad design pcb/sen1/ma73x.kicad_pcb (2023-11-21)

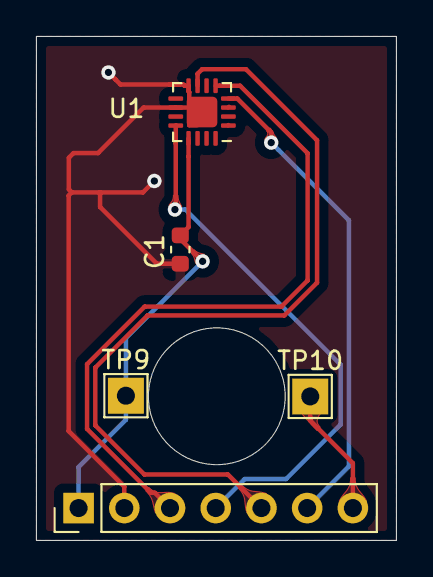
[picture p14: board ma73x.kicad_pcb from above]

Board: 2 copper layers, 20.0 x 28.0 mm, 5 parts (0 on the bottom side), 7 nets.

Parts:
C1: C; C_0603_1608Metric
J1: Conn_01x07; PinHeader_1x07_P2.54mm_Vertical
TP9: Laser Pow; TestPoint_THTPad_2.0x2.0mm_Drill1.0mm
TP10: Laser GND; TestPoint_THTPad_2.0x2.0mm_Drill1.0mm
U1: MA732; QFN-16-1EP_3x3mm_P0.5mm_EP1.7x1.7mm

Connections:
/3.3V: C1.1, J1.1, TP9.1, U1.13
/CLK: J1.4, U1.12
/CS: J1.3, U1.5
/GND: C1.2, J1.2, U1.8, U1.10, U1.17
/LSR: J1.7, TP10.1
/MISO: J1.5, U1.7
/MOSI: J1.6, U1.4

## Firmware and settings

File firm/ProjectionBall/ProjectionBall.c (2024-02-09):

/*
 *  	ProjectionBall.c
 *
 *  Copyright (c) 2023
 *  K.Watanabe, Crescentt
 *  Released under the MIT license
 *  http://opensource.org/licenses/mit-license.php
 *
 */

#include <stdio.h>
#include <stdbool.h>
#include "pico/stdlib.h"
#include "pico/multicore.h"
#include "hardware/spi.h"
#include "hardware/i2c.h"
#include "hardware/timer.h"
#include "hardware/pwm.h"
#include "hardware/rtc.h"
#include "hardware/watchdog.h"
#include "ProjectionBall.h"
#include "rtc_rv8803.h"
#include "rtc_sd30XX.h"
#include "encoder_ma732.h"
#include "motor_ctrl.h"
#include "path_ctrl.h"
#include "flash_ctrl.h"
#include "console.h"


static semaphore_t 	sem;
static bool 		CtrlEventFlg = false;
static bool 		PathEventFlg = false;
struct repeating_timer control_timer;
struct repeating_timer path_timer;
alarm_pool_t* 		core0Alarm;
alarm_pool_t* 		core1Alarm;

bool control_timer_callback(struct repeating_timer *t)
{    
	if(CtrlEventFlg == false)
		CtrlEventFlg = true;
	else
	{
		gpio_put(PIN_STBY, 0);
		cancel_repeating_timer(&control_timer);
		puts("Control Timer Call Err");
	}
    return true;
}

bool path_timer_callback(struct repeating_timer *t)
{    
	if(PathEventFlg==false)
		PathEventFlg=true;
	// else
	// {
	// 	cancel_repeating_timer(&path_timer);
	// 	puts("Path Timer Call Err");
	// }
    return true;
}

void core1_main()
{

	core1Alarm = alarm_pool_create(1, 4);
	//irq_set_priority(0,0x00);
	alarm_pool_add_repeating_timer_us(core1Alarm, 80, control_timer_callback, NULL, &control_timer);//80us
	watchdog_enable(1, 1);
	//Control Loop
	while (true)
    {
		//Control Event
		if( CtrlEventFlg == true )
		{
			CtrlEventFlg = false;
			MotorCtrlLoop();
			UpdateUserButton();
			if( IsResetEnable()==false)
				watchdog_update();							
		}
	}
}

void core0_main()
{	

	core0Alarm = alarm_pool_create(0, 4);
	alarm_pool_add_repeating_timer_ms(core0Alarm, 320, path_timer_callback, NULL, &path_timer);
	while (true)
	{
		
		if( PathEventFlg == true)
		{
			PathEventFlg = false;
			PathCtrlLoop();				
			ConsoleGetString();
#ifdef ENABLE_DEBUG_OUTPUT
			DebugMotorCtrl();
#endif
			
		}
	
	}	
}

void ioInit()
{
	//Motor Direction Pin
	gpio_init(PIN_STBY);
	gpio_init(PIN_LSR);
	gpio_init(PIN_ERR);
	gpio_init(PIN_A1);
	gpio_init(PIN_A2);
	gpio_init(PIN_B1);
	gpio_init(PIN_B2);
	gpio_init(PIN_MODE);
	gpio_init(PIN_PATTERN);	
    gpio_set_dir(PIN_STBY, GPIO_OUT);
	gpio_set_dir(PIN_LSR, GPIO_OUT);
	gpio_set_dir(PIN_ERR, GPIO_OUT);
	gpio_set_dir(PIN_A1, GPIO_OUT);
    gpio_set_dir(PIN_A2, GPIO_OUT);
    gpio_set_dir(PIN_B1, GPIO_OUT);
    gpio_set_dir(PIN_B2, GPIO_OUT);
	gpio_set_dir(PIN_MODE, GPIO_IN);
    gpio_set_dir(PIN_PATTERN, GPIO_IN);
	gpio_put(PIN_STBY, 0);
	gpio_put(PIN_LSR, 0);
	gpio_put(PIN_ERR, 1);//Check LED 
	gpio_put(PIN_A1, 0);
	gpio_put(PIN_A2, 0);
	gpio_put(PIN_B1, 0);
	gpio_put(PIN_B2, 0);
    gpio_pull_up(PIN_MODE);
    gpio_pull_up(PIN_PATTERN);
	
	// PWM initialisation
	gpio_set_function(PIN_PWM_A, GPIO_FUNC_PWM);
    gpio_set_function(PIN_PWM_B, GPIO_FUNC_PWM);


    // SPI initialisation
    spi_init(SPI_PORT, 8000*1000);//10MHz
#ifdef USE_MA732
	spi_set_format(SPI_PORT, 8, SPI_CPOL_0, SPI_CPHA_0, SPI_MSB_FIRST);
#endif
#ifdef USE_AS5048A
	spi_set_format(SPI_PORT, 8, SPI_CPOL_0, SPI_CPHA_1, SPI_MSB_FIRST);
#endif
    gpio_set_function(PIN_MISO, GPIO_FUNC_SPI);
    gpio_set_function(PIN_CS1,   GPIO_FUNC_SIO);
    gpio_set_function(PIN_SCK,  GPIO_FUNC_SPI);
    gpio_set_function(PIN_MOSI, GPIO_FUNC_SPI);
    

    // Chip select initialise
    gpio_init(PIN_CS1);
	gpio_init(PIN_CS2);
	gpio_set_dir(PIN_CS1, GPIO_OUT);
	gpio_set_dir(PIN_CS2, GPIO_OUT);
    gpio_put(PIN_CS1, 1);
    gpio_put(PIN_CS2, 1);
	sleep_ms(5);
    gpio_put(PIN_ERR, 0);

    // I2C Initialisation at 100Khz
    i2c_init(i2c0, 200*1000);    
    gpio_set_function(I2C_SDA, GPIO_FUNC_I2C);
    gpio_set_function(I2C_SCL, GPIO_FUNC_I2C);
    gpio_pull_up(I2C_SDA);
    gpio_pull_up(I2C_SCL);

	//UART
    uart_init(UART_ID, 2400); 
    gpio_set_function(PIN_TX, GPIO_FUNC_UART);
    gpio_set_function(PIN_RX, GPIO_FUNC_UART);
    uart_set_baudrate(UART_ID, BAUD_RATE);
    uart_set_hw_flow(UART_ID, false, false);
    uart_set_format(UART_ID, DATA_BITS, STOP_BITS, PARITY);
    uart_set_fifo_enabled(UART_ID, false);    
    irq_set_exclusive_handler(UART0_IRQ, OnUartRx);
    irq_set_enabled(UART0_IRQ, true);

    // Now enable the UART to send interrupts - RX only
    uart_set_irq_enables(UART_ID, true, false);

	//RTC Init
	rtc_init();
  

}

int main()
{
    	
	stdio_init_all();
	sem_init(&sem, 1, 1);	
	ioInit();

#ifdef ENABLE_FLASH_TEST
	TestFlashReadWrite();
#endif

	if(watchdog_caused_reboot())
	{
		sleep_ms(1000);			
	}

	MotorCtrlInit();

#ifdef ENABLE_ENCODER_CHECK_MODE
	uint16_t encVal0, encVal1;
	while(1)
	{
		sleep_ms(300);
		MA732ReadAngleBit(PIN_CS1, &encVal0);
		MA732ReadAngleBit(PIN_CS2, &encVal1);
		printf("Val0: %d, Val1:%d\n",encVal0>>2,encVal1>>2);		
	}
#endif

	sleep_ms(500);
    printf("\r\n\r\n ProjectionBall Unit"VER_STR" \r\n");
	printf("[Build: "__DATE__"]\r\n");

#ifdef USE_RTC_RV8803
	if( IsRtcBOR() == true )
		printf("RTC was Cleared. Check Battery & Set Datetime!\r\n");
#endif
	GetDateTime();

	//Update HW RTC
	UpdateHwRtc();
	RestoreUserData();
	ClearBuffer();
	sleep_ms(500);	

	multicore_launch_core1(core1_main);		
	core0_main();

    return 0;
}

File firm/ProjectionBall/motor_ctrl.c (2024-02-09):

/*
 *  	motor_ctrl.c
 *
 *  Copyright (c) 2023
 *  K.Watanabe, Crescentt
 *  Released under the MIT license
 *  http://opensource.org/licenses/mit-license.php
 *
 */
#include <stdio.h>
#include <stdbool.h>
#include "pico/stdlib.h"
#include "hardware/pwm.h"
#include "ProjectionBall.h"
#include "motor_ctrl.h"
#include "path_ctrl.h"
#include "path_const.h"
#include "encoder_as5048a.h"
#include "encoder_ma732.h"
#include "rtc_rv8803.h"
#include "rtc_sd30XX.h"

#define 	MAX_LOG_LEN				1500

#ifdef ENABLE_STEP_CMD
	#define 	STEP_START_LEN		500
	#define 	STEP_END_LEN		1000
#endif



#define X_CENTER0					2500//2500
#define X_CENTER1					2000//2000
#define PWM_MAX_DUTY				2048

#define T_LIMIT_MAXERR_N			-1000
#define T_LIMIT_MAXERR_P			+1000
#define T_LIMIT_DIV					20	
#define T_LIMIT_START_CNT			800
#define T_LIMIT_START_CNT_HALF		(T_LIMIT_START_CNT/2)

#ifdef ENABLE_RUNAWAY_DETECTION
	#define MAX_ERR_COUNT			800
	#define POS_ERR_RANGE			100
	#define T_LIMIT_DIV2			10	
#endif

struct MotorCtrlStruct		motorControl[2];
struct MotorLogStruct		motorLog[2][MAX_LOG_LEN];
static uint					pwm_slice_num;
volatile static uint 		InitCount;//Torque Limit for suppress runaway in start up
volatile static uint32_t	ControlCount;
volatile static uint32_t 	ErrCount;
volatile static bool		isPause = false;
volatile static bool		isPause_old = false;
volatile static int32_t 	kpGain;
volatile static int32_t 	kdGain;
volatile static int32_t 	ikiGain;
volatile static uint8_t		uPrjAngle;
volatile static int32_t		prjAngle;

inline static void getResponse();
inline static void shiftBuffer();
inline static void calcResponse();
inline static void getCommand();
inline static void calcErr();
inline static void calcTrqCommand();
inline static void setMotorOutput();
inline static void calcVelErr();
inline static void logSave();




void MotorCtrlInit()
{	
#ifdef USE_MA732
	//Set Filter Setting
	MA732WriteReg(PIN_CS1, MA732_REG_FW,84);//def:64:84::80
	MA732WriteReg(PIN_CS2, MA732_REG_FW,84);//def:64:84::80
#endif

	motorControl[0].x_cen=X_CENTER0;
	motorControl[1].x_cen=X_CENTER1;
	
	motorControl[0].x_sum=0;
	motorControl[1].x_sum=0;
	
	InitCount = 0;
	ControlCount = 0;
	ErrCount = 0;

	kpGain = KP;
	kdGain = KD;
#ifdef ENABLE_I
	ikiGain = IKI;
#endif
#ifndef DISABLE_MOTOR
	gpio_put(PIN_STBY, 1);//1:DRV ON, 0:DRV OFF
	gpio_put(PIN_LSR, 1);//1:ON, 0:OFF
	
	
	//Init Pwm Setting	
	pwm_slice_num = pwm_gpio_to_slice_num(2);
	pwm_set_clkdiv(pwm_slice_num, 3.8);//16kHz
    pwm_set_wrap(pwm_slice_num, PWM_MAX_DUTY);
	pwm_set_chan_level(pwm_slice_num, PWM_CHAN_A, 0);
    pwm_set_chan_level(pwm_slice_num, PWM_CHAN_B, 0);
	pwm_set_enabled(pwm_slice_num, true);	
#endif
}


void __time_critical_func(MotorCtrlLoop)()
{	
	
	if(isPause==true)
	{
		gpio_put(PIN_STBY, 0);//1:DRV ON, 0:DRV OFF
		gpio_put(PIN_LSR, 0);//1:ON, 0:OFF
		return;
	}
		
	getResponse();		
	shiftBuffer();
	calcResponse();
	getCommand();
	calcErr();
	calcTrqCommand();
	setMotorOutput();
	logSave();
	calcVelErr();
	
#ifdef ENABLE_STEP_CMD
	if(InitCount<T_LIMIT_START_CNT)
	{
		//Nothing todo 
	}
	else if(ControlCount<MAX_LOG_LEN)
	{
		ControlCount++;
	}		
	else
	{
		gpio_put(PIN_STBY, 0);
	}
#endif

}

void DebugMotorCtrl()
{
	// float angf=0.0f;
	// angf=(float)motorControl[0].x_res/(0x3FFF)*360.0f;	
	// printf("Angle:%1.1f\n",angf);
	
	// printf("res:%d, \t tau:%d \t err:%d \n",
		// motorControl[0].x_res,
		// motorControl[0].trq_out,
		// motorControl[0].x_err);
#ifdef ENABLE_STEP_CMD
	if(ControlCount>(MAX_LOG_LEN-1))
	{
		for(int i=0; i<MAX_LOG_LEN; i++)
		{
			printf("%d,%d,%d,%d, \t%d,%d,%d,%d\n",
				motorLog[0][i].x_cmd,
				motorLog[0][i].x_res,
				motorLog[0][i].x_sum,
				motorLog[0][i].trq_out,
				motorLog[1][i].x_cmd,
				motorLog[1][i].x_res,
				motorLog[1][i].x_sum,
				motorLog[1][i].trq_out
				);			
		}
		
	}
	while(1);
#endif

#if defined( ENABLE_SIN_CMD) ||  defined (ENABLE_DEBUG_INFO)
	printf("\t%d,%d,%d,%d, \t%d,%d,%d,%d\n",
				motorControl[0].x_cmd,
				motorControl[0].x_res,
				motorControl[0].x_sum,
				motorControl[0].trq_out,
				motorControl[1].x_cmd,
				motorControl[1].x_res,
				motorControl[1].x_sum,
				motorControl[1].trq_out
				);	
	DebugPathCtrl();		
#endif

}

void MotorCtrSetCenterPos(int32_t pos0, int32_t pos1)
{
	motorControl[0].x_cen=X_CENTER0 + pos0;
	motorControl[1].x_cen=X_CENTER1 + pos1;
	printf("CenOff: %d, %d CenPos: %d, %d\r\n", pos0, pos1, motorControl[0].x_cen,motorControl[1].x_cen);
}

void MotorCtrGetCenterPos(int32_t *pos0, int32_t *pos1)
{
	*pos0 = motorControl[0].x_cen;
	*pos1 = motorControl[1].x_cen;
}

void SetPause(bool pause)
{
	isPause = pause;

	if(isPause!=isPause_old)
	{
		printf(" *Set Pause Enabled:%d->%d\r\n", isPause_old, isPause);
		if(isPause==false)
		{
			InitCount = 0;
			ControlCount = 0;
			ErrCount = 0;
			motorControl[0].x_sum = 0;
			motorControl[1].x_sum = 0;	
			gpio_put(PIN_STBY, 1);//1:DRV ON, 0:DRV OFF
			gpio_put(PIN_LSR, 1);//1:ON, 0:OFF
		}
		isPause_old = isPause;
	}	
}

void SetGain(int32_t kp, int32_t kd, int32_t iki)
{
	kpGain = kp;
	kdGain = kd;
	ikiGain = iki;
}

void GetGain(int32_t *kp, int32_t *kd, int32_t *iki)
{
	*kp = kpGain;
	*kd = kdGain;
	*iki = ikiGain;
}

void SetProjectionAngle( int32_t deg )
{	
	prjAngle = deg/((int)360/TRIG_FUNCTION_LEN);
	prjAngle = prjAngle*((int)360/TRIG_FUNCTION_LEN);
	uPrjAngle = prjAngle/((int)360/TRIG_FUNCTION_LEN);
	SetRtcRam(PRJ_DEG_SRAM, uPrjAngle);
}

void GetProjectionAngle(int32_t *deg)
{
	*deg = prjAngle;
}

inline static void getResponse()
{
#ifdef USE_MA732
	MA732ReadAngleBit(PIN_CS1, &motorControl[0].encRaw);
	MA732ReadAngleBit(PIN_CS2, &motorControl[1].encRaw);
#endif
#ifdef USE_AS5048A
	AS5048AReadAngleBit(PIN_CS1, &motorControl[0].encRaw);
	AS5048AReadAngleBit(PIN_CS2, &motorControl[1].encRaw);
#endif
}

inline static void shiftBuffer()
{
	
	for(size_t i=0; i< (ENCODER_BUFFER_SIZE-1); i++)
	{
		motorControl[0].encBuf[ENCODER_BUFFER_SIZE-(i+1)]
			=motorControl[0].encBuf[ENCODER_BUFFER_SIZE-(i+2)];
		motorControl[1].encBuf[ENCODER_BUFFER_SIZE-(i+1)]
			=motorControl[1].encBuf[ENCODER_BUFFER_SIZE-(i+2)];			
	}
	
	motorControl[0].encBuf[0]=motorControl[0].encRaw;
	motorControl[1].encBuf[0]=motorControl[1].encRaw;
}

inline static void calcResponse()
{
	int32_t sum[2]={0};
	
	for(size_t i=0; i<ENCODER_BUFFER_SIZE; i++)
	{
		sum[0]+=motorControl[0].encBuf[i];
		sum[1]+=motorControl[1].encBuf[i];		
	}
	sum[0]=(sum[0]/ENCODER_BUFFER_SIZE);
	sum[1]=(sum[1]/ENCODER_BUFFER_SIZE);
	
	motorControl[0].x_res=(sum[0]>>2);//16bit->14bit
	motorControl[1].x_res=(sum[1]>>2);//16bit->14bit	
}

inline static void getCommand()
{
	//Command
	motorControl[0].p_cmd = 0;
	motorControl[1].p_cmd = 0;
	motorControl[0].dx_cmd = 0;
	motorControl[1].dx_cmd = 0;
	motorControl[0].enableLaser = 0;

	GetPathCmd(&motorControl[0].p_cmd, &motorControl[1].p_cmd, &motorControl[0].enableLaser );
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

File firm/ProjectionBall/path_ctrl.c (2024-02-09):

/*
 *  	path_ctrl.c
 *
 *  Copyright (c) 2023
 *  K.Watanabe, Crescentt
 *  Released under the MIT license
 *  http://opensource.org/licenses/mit-license.php
 *
 */
#include <stdio.h>
#include <stdlib.h>
#include <string.h>
#include <stdbool.h>
#include "pico/stdlib.h"
#include "pico/multicore.h"
#include "hardware/rtc.h"
#include "hardware/watchdog.h"
#include "ProjectionBall.h"
#include "motor_ctrl.h"
#include "path_ctrl.h"
#include "path_const.h"
#include "path_font.h"
#include "rtc_rv8803.h"
#include "rtc_sd30XX.h"
#include "flash_ctrl.h"

#define REPEAT_NUM  5
#define IN_POS_MAX  48
#define IN_POS_MIN  -IN_POS_MAX


#define ONE_STROKE_MODE_SPEED   5
#define ONE_STROKE_MODE_WAIT    30

typedef struct SettingData
{
    int16_t     pauseTime;
    int16_t     resumeTime;
    char        userString[USER_STRING_LEN];
}SettingData_t;

typedef struct CalibrationData
{
    int32_t     x_cen0;
    int32_t     x_cen1;
}CalibrationData_t;

static SettingData_t settingData;
static CalibrationData_t calibrationData;


static uint8_t SelectPattern = PATTERN_STAR;
static uint8_t SelectMode = MODE_PATTERN_ALWAYS_ON;
static int32_t laser_stroke_cnt = 0;
static int32_t rotate_deg = 0;
static int32_t step = 0;
static int32_t allstep = 0;
static int32_t repeat_cnt = 0;
static uint8_t string_cnt = 0;
static bool	   enablePauseResume = false;
static int32_t x_cen0, x_cen1;
static int16_t resumeTime;
static int16_t pauseTime;

static char PathString[USER_STRING_LEN]={'\0'};
static char SelString[USER_STRING_LEN]={'\0'};
static char TimeString[8]={'\0'};
static uint8_t date_y=0;
static uint8_t date_m=0;
static uint8_t date_d=0;
static uint8_t time_h=0;
static uint8_t time_m=0;
static uint8_t time_s=0;

static uint8_t  strShift = 0;
static uint8_t  strShiftOld = 0;
static uint8_t  allStrShiftFlg = 0;
static uint8_t  strLength = 0;

static bool pattern_sw_old = 1;
static bool mode_sw_old = 1;
static bool pattern_sw = 1;
static bool mode_sw = 1;
static bool pattern_update = false;
static bool mode_update = false;

inline static void checkUserButton();
inline static void getPatternPath(int32_t *step, int32_t *allstep, int32_t *x, int32_t *y, bool *lsr);
inline static void getStringPath(char *str, uint8_t *strcnt, int32_t *step, int32_t *allstep, int32_t *x, int32_t *y, bool *lsr);
inline static void getDateString(char *str);
inline static void getTimeString(char *str);
inline static void updateDateTime();


void __time_critical_func(GetPathCmd)(int32_t *cmd0, int32_t *cmd1, bool *laser)
{
    int32_t x0 = 0, x1 = 0;

    bool lsr = false;

    switch(SelectMode)
    {
        case MODE_PATTERN_ALWAYS_ON:
            getPatternPath(&step, &allstep, &x0, &x1, &lsr);
            break;

        case MODE_PATTERN_ONE_STROKE:
            getPatternPath(&step, &allstep, &x0, &x1, &lsr);
            if( lsr == 1 && laser_stroke_cnt <= step )
                lsr = 0;            
            break;

        case MODE_PATTERN_ROTATION:
            getPatternPath(&step, &allstep, &x0, &x1, &lsr);
            x0 = CalcCosVal(rotate_deg, x0);
            break;

        case MODE_WATCH:
            getTimeString(TimeString);
            getStringPath(TimeString, &string_cnt, &step, &allstep, &x0, &x1, &lsr);
            break;

        case MODE_DATE:
            getDateString(TimeString);
            getStringPath(TimeString, &string_cnt, &step, &allstep, &x0, &x1, &lsr);
            break;

        case MODE_MSG:
            if(strlen(PathString)>MAX_STRING_LEN) // Auto Scroll
            {
                if( strShift != strShiftOld )
                {
                    string_cnt = 0; 
                    step = 0;
                    strShiftOld = strShift;
                }
                getStringPath(SelString, &string_cnt, &step, &allstep, &x0, &x1, &lsr);   
            }
            else // Projection at once
            {
                getStringPath(PathString, &string_cnt, &step, &allstep, &x0, &x1, &lsr);   
            }                     
            break;

        default:
            break;
    }

#ifdef ENABLE_SIN_CMD
	x0 = CalcSinVal(rotate_deg,SIN_CMD_AMP);
	x1 = CalcSinVal(rotate_deg,SIN_CMD_AMP);
#endif 

    *cmd0 = x0;
    *cmd1 = x1;
    *laser = lsr;

    //Check In Pos
#ifdef ENABLE_IN_POS
    if( motorControl[0].x_err > IN_POS_MIN && motorControl[0].x_err <IN_POS_MAX 
    &&  motorControl[1].x_err > IN_POS_MIN && motorControl[1].x_err <IN_POS_MAX )
        repeat_cnt++;
#else
    repeat_cnt++;
#endif

    if(repeat_cnt>=REPEAT_NUM)
    {
        step++;
        repeat_cnt = 0;
    }

    if( SelectMode == MODE_WATCH || SelectMode == MODE_DATE || SelectMode == MODE_MSG)
    {
        if(CheckNextStrFlg()==true)
            repeat_cnt = -8;
        else if(CheckFirstStrFlg()==true)
            repeat_cnt = -16;
    }
}

void PathCtrlLoop()
{
    checkUserButton();
    updateDateTime();
        
    switch(SelectMode)
    {
        case MODE_PATTERN_ONE_STROKE:
            laser_stroke_cnt = laser_stroke_cnt + ONE_STROKE_MODE_SPEED;
            if( laser_stroke_cnt > (allstep + ONE_STROKE_MODE_WAIT) )
                laser_stroke_cnt = 0;
            break;

        case MODE_PATTERN_ROTATION:        
            rotate_deg = rotate_deg + 3;
            if(rotate_deg>=TRIG_FUNCTION_LEN)
                rotate_deg = 0;
            break;

        case MODE_MSG:
            memset(SelString, '\0', USER_STRING_LEN);
            strLength = strlen(PathString);            
            if(strlen(PathString)>MAX_STRING_LEN)
            {
                memset(SelString, ' ', MAX_STRING_LEN);
                if( 0<= strShift && strShift < MAX_STRING_LEN)
                {
                    strncpy(	&SelString[MAX_STRING_LEN-strShift-1],
                                &PathString[0],
                                strShift+1);
                }
                else if( MAX_STRING_LEN <= strShift && strShift < (strLength+1) )
                {
                    strncpy(	SelString,
                                &PathString[strShift-MAX_STRING_LEN+1],
                                MAX_STRING_LEN);
                }
                else if( (strLength+1) <= strShift && strShift <= (MAX_STRING_LEN+strLength-1) )
                {
                    strncpy(	SelString,
                                &PathString[strShift-MAX_STRING_LEN+1],
                                strLength+MAX_STRING_LEN-strShift-1);
                }

                strShift++;
                if( (strLength+MAX_STRING_LEN-1)<strShift)
                    strShift = 0;
                
            }

            break;

        default:
#ifdef ENABLE_SIN_CMD
            rotate_deg = rotate_deg + 6;
            if(rotate_deg>=TRIG_FUNCTION_LEN)
                rotate_deg = 0;
#endif
            break;
    }    
}
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

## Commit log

2023-11-21 Add PCB Files
    [ma73x-B_Cu.gbl, ma73x-B_Mask.gbs, ma73x-B_Paste.gbp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]
2023-11-21 Add Footprint Files
2024-02-09 Release v1.3
    ・Improve button response
    ・Improve start up stability
    Release v1.3
    [ProjectionBall.c, ProjectionBall.h, motor_ctrl.c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]
